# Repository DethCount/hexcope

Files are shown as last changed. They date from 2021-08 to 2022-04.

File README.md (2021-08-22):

# Hexcope - **Work in Progress**

3d printable hex pattern parabolic mirror for telescope \
20x20x20 cm parts \

## Primary mirror
19 x 20cm side hexagonal mirrors \
https://www.gifi.fr/product/id/557688/miroir-sticker-hexagonal-x-3

## Secondary mirror - **Work in Progress**
Allows for Newton setup (with basis central hex on) \

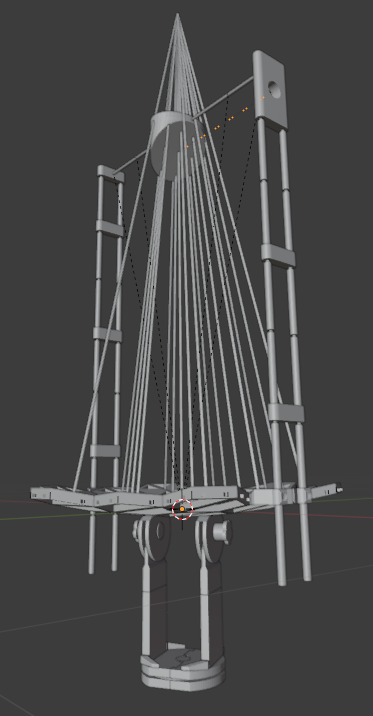
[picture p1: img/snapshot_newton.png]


or Ritchley-Chretien setup (with camera at basis center)

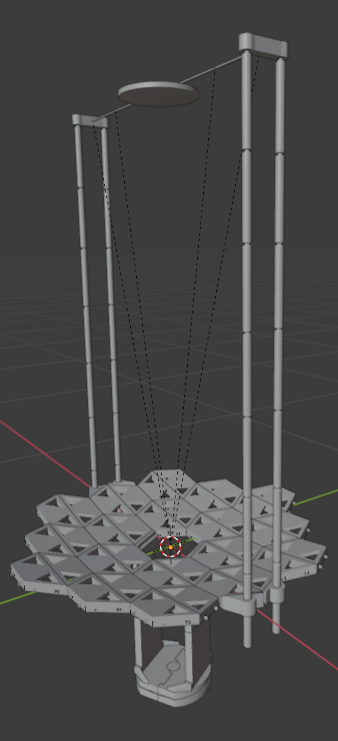
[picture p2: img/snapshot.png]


1 x 10cm radius round mirror \
https://www.gifi.fr/product/id/557686/miroir-sticker-rond-x-3

## Telescope basis
missing instrument plate and central hex for Newton setup

## Running scripts in Blender
Launch Blender (throw a terminal if you need to debug) \
in the Scripting tab open support.py and run it \
then open basis.py and run it

OR
in terminal:
blender.exe -P support.py -P basis.py

## Gcode files
DM_ is for Dagoma Magis 3d printer
DD_ is for Dagoma DiscoEasy200

## Scaling
Hexcope can be scaled by primary mirror radius hyperparameter "n" (number of hexagons) \
e.g : n = 4, f = 16 (= 1.6m) \
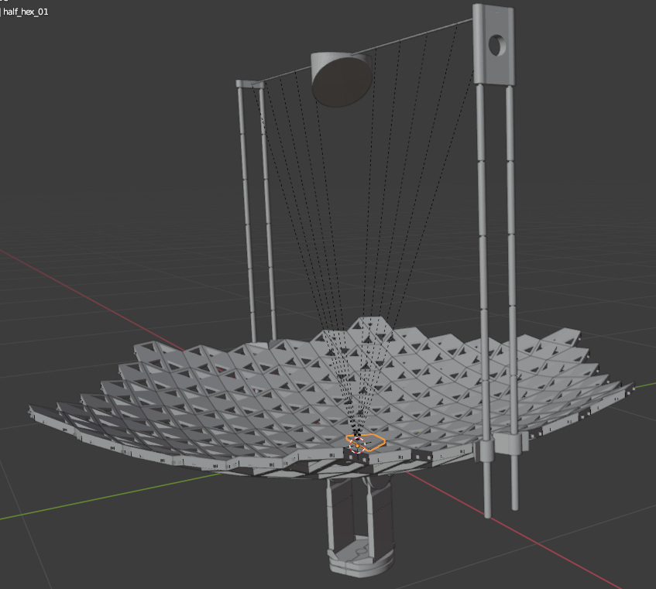
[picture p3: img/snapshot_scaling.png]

\
and by number of support arms \
e.g : support_arm_n = 6 \
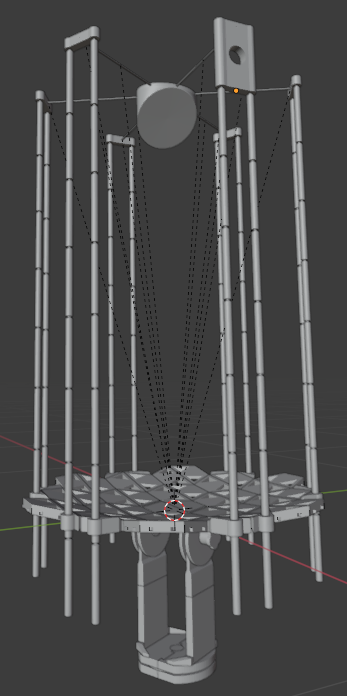
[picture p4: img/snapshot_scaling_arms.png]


## Assembling
Just clip parts together. For mirror parts, use horizontal lines, not numbers.

Primary mirror PLA parts can be soldered using filament \
https://youtu.be/Q-PgjTYsAFY

## Printing
(e.g: Dagoma DiscoEasy200) \
Layer height: 0.3mm \
Infill density: 10% \
Print speed: 75 mm/s \
Infill speed: 80 mm/s \
Outer wall speed: 50 mm/s \
Inner wall speed: 70 mm/s \
Top / Bottom speed: 70 mm/s \
Travel speed: 100 mm/s \
Initial layer speed: 20 mm/s \
Number of slower layers: 1 \
Support: touching buildplate \
Build plate adhesion type: skirt \
Skirt line count: 3 \
Skirt distance: 2mm \

- Basis: 1.326kg, 490m, 64h30
    - 2 x plate bottom: 96g, 33m, 3h30
    - 1 x plate axis: 205g, 70m, 7h
    - 2 x plate top: 96g, 33m, 3h30
    - 2 x leg: 113g, 39m, 5h  (support: everywhere)
    - 4 x foot: 10g, 4m, 0h30
    - 2 x arm: 79g, 27m, 4h
    - 2 x wheel: 135g, 46m, 6h (print vertically, bottom up)
    - 2 x screw: 18g, 6m, 2h30 (0.1mm layer height)
    - 2 x screw cap: 25g, 9m, 3h30  (0.1mm layer height)
- Primary mirror (n=0, newton): 1152g, 396m, 51h
    - 2 x center half hex: 47g, 16m, 1h30
    - 16 x half hex: 67g, 23m, 3h
- OR Primary mirror (n=1, newton): 2506g, 860m, 111h
    - 2 x center half hex: 47g, 16m, 1h30
    - 36 x half hex: 67g, 23m, 3h
- Secondary mirror support (n=0, f=16, arm_n=2, newton): 0,795kg, 300m, 100h30
    - 4 x arm block: 22g, 8m, 1h
    - 30 x arm: 18g, 7m, 2h30 (orientation: bottom up, layer height: 0.1mm, experimental: use adaptative layers, infill density: 30%)
    - 1 x arm head 0 with eyepiece support: 128g, 44m, 15h30 (orientation: little spider screw up, layer height: 0.1mm, support: touching buildplate)
    - 1 x arm head: 34g, 12m, 4h30 (orientation: little spider screw up, layer height: 0.1mm)
    - 1 x 2 spider arms 0: 5g, 2m, 1h30 (orientation: bottom up, layer height: 0.1mm, experimental: use adaptative layers, infill density: 30%)
- OR Secondary mirror support (n=1, f=16, arm_n=2, newton): 0,800kg, 302m, 102h
    - 4 x arm block: 22g, 8m, 1h
    - 30 x arm: 18g, 7m, 2h30 (orientation: bottom up, layer height: 0.1mm, experimental: use adaptative layers, infill density: 30%)
    - 1 x arm head 0 with eyepiece support: 128g, 44m, 15h30 (orientation: little spider screw up, layer height: 0.1mm, support: touching buildplate)
    - 1 x arm head: 34g, 12m, 4h30 (orientation: little spider screw up, layer height: 0.1mm)
    - 1 x 2 spider arms 0: 5g, 2m, 1h30 (orientation: bottom up, layer height: 0.1mm, experimental: use adaptative layers, infill density: 30%)
    - 1 x 2 spider arms 1: 5g, 2m, 1h30 (orientation: bottom up, layer height: 0.1mm, experimental: use adaptative layers, infill density: 30%)
- Secondary mirror (f=16, arm_n=2, newton): 177g, 60m, 16h (disable support, experimental: use adaptative layers, layer height: 0.1mm)

## Current prototype state
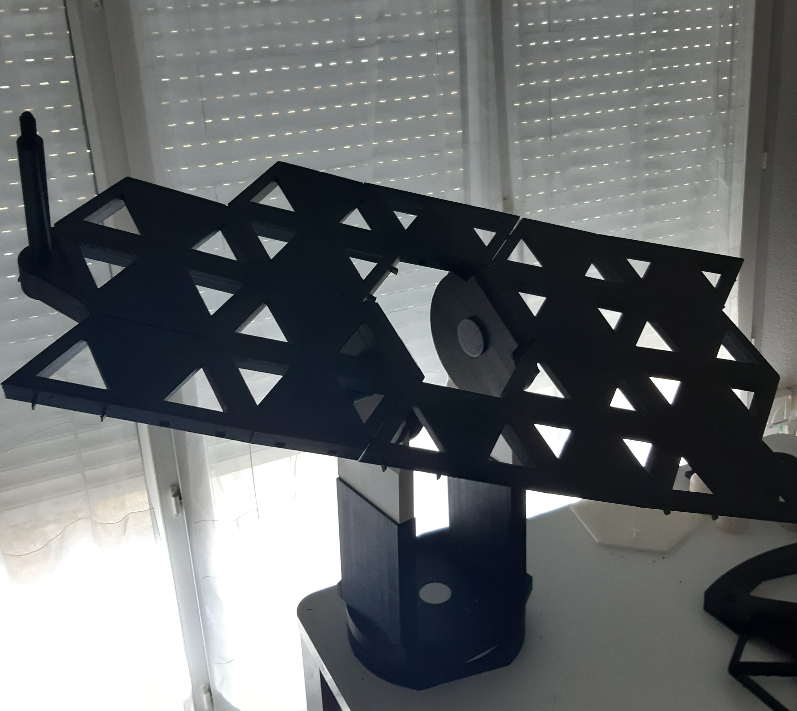
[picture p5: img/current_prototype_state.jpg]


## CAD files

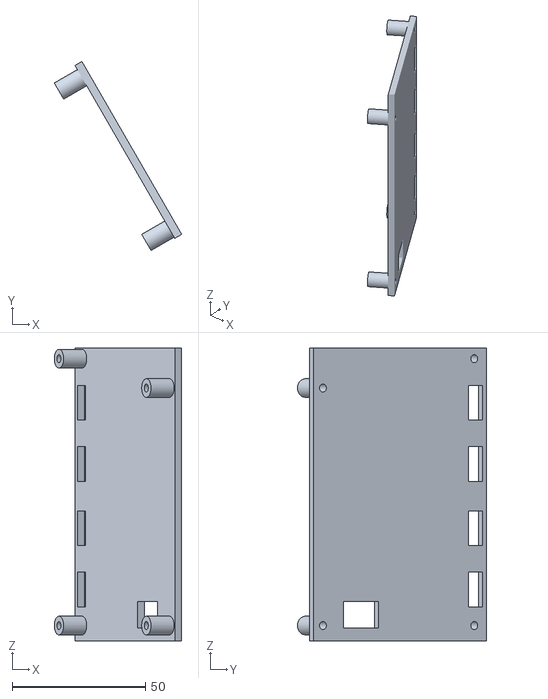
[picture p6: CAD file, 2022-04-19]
stl/basis_mainboard_cover.stl
47.8 x 70.8 x 109.8

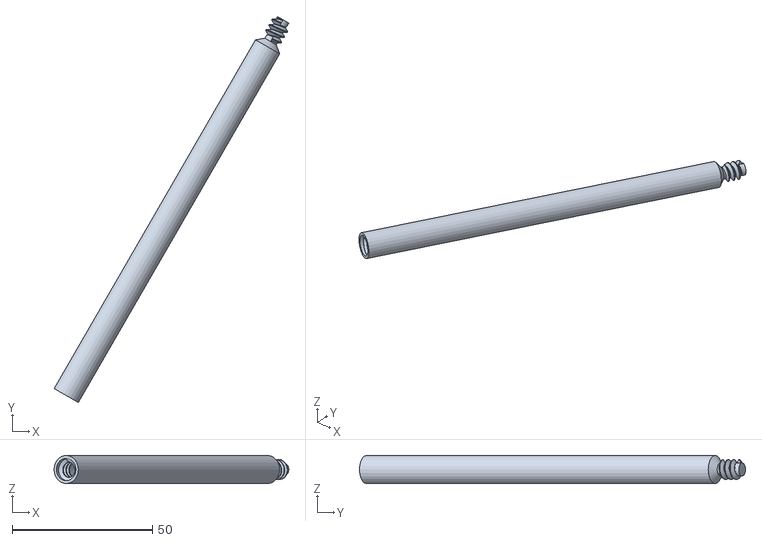
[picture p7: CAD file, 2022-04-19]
stl/support_spider_arm_4_0.stl
83.6 x 137.5 x 9.98

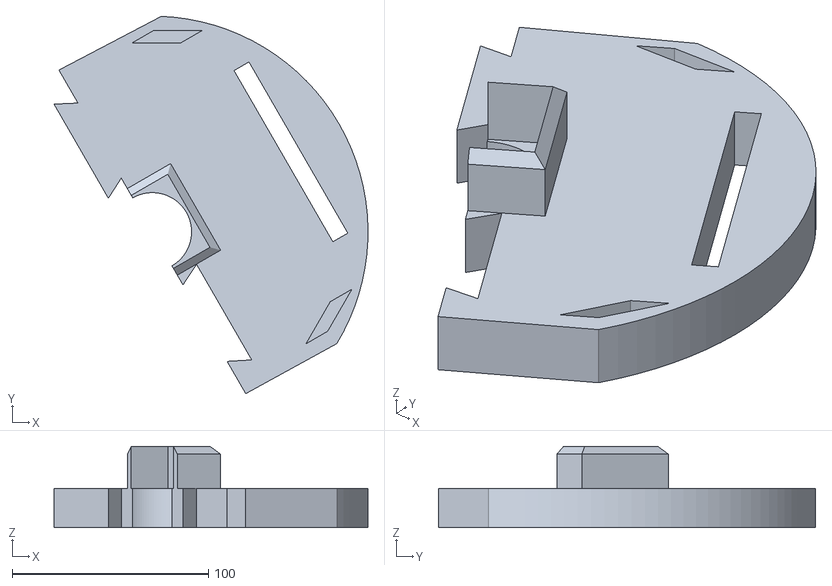
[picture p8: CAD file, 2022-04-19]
stl/basis_plate_top_r.stl
160.1 x 192.4 x 41.5

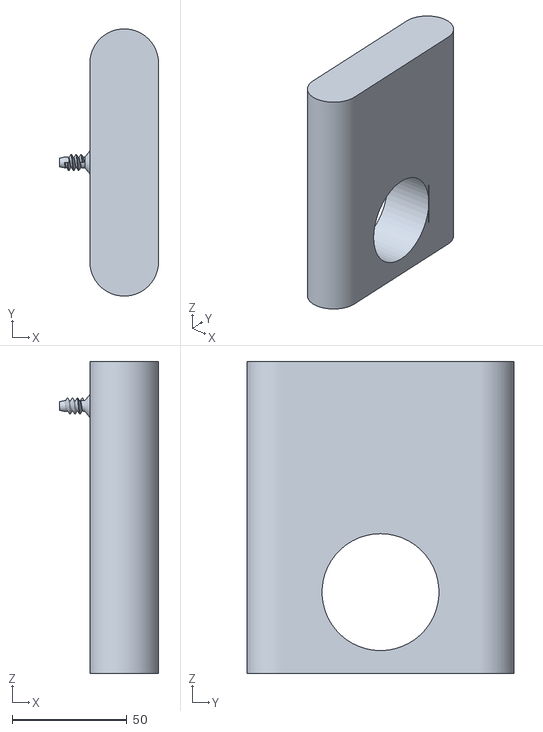
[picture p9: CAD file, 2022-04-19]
stl/support_arm_head_0.stl
43.3 x 116.6 x 136.1

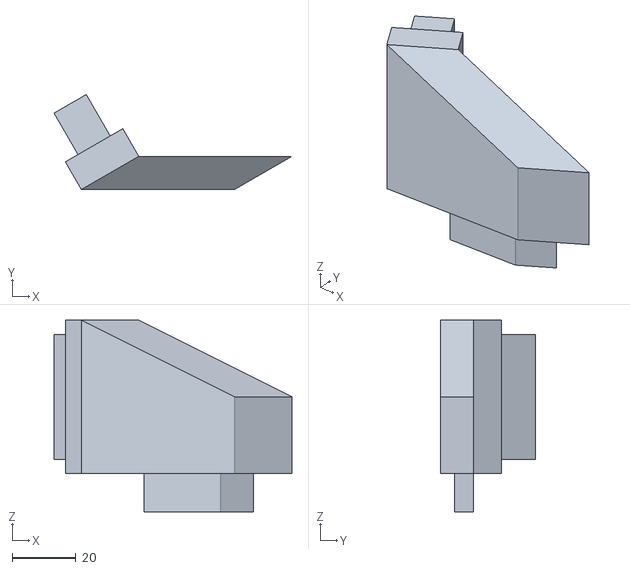
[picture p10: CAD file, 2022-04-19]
stl/basis_foot_ll.stl
74.6 x 29.8 x 60.0

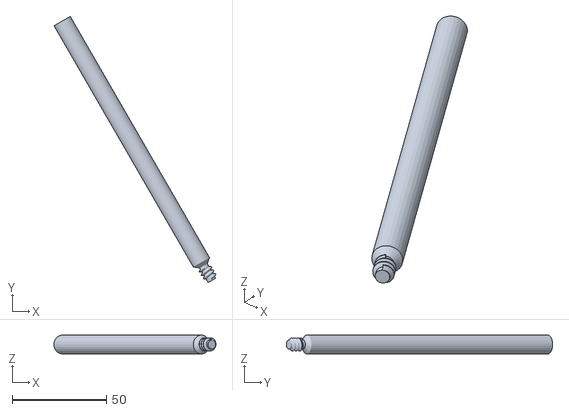
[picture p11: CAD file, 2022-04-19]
stl/support_spider_arm_2_1.stl
86.0 x 141.3 x 9.98

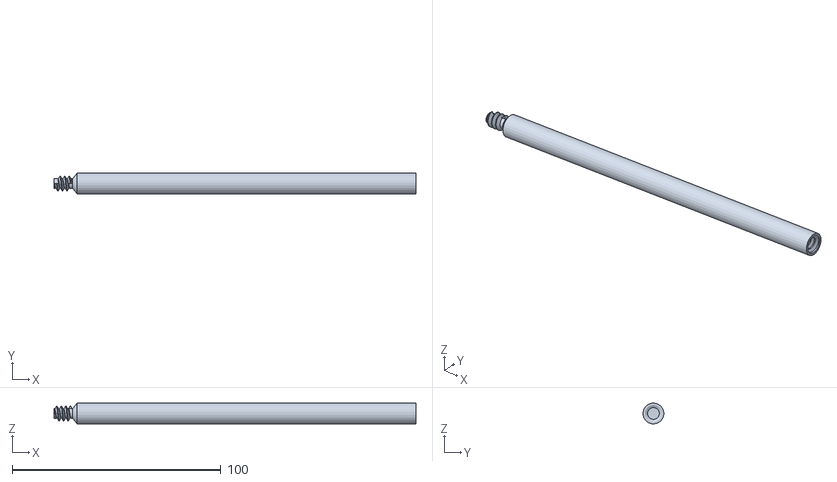
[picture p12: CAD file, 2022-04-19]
stl/support_spider_arm_0_0.stl
173.2 x 9.96 x 9.98

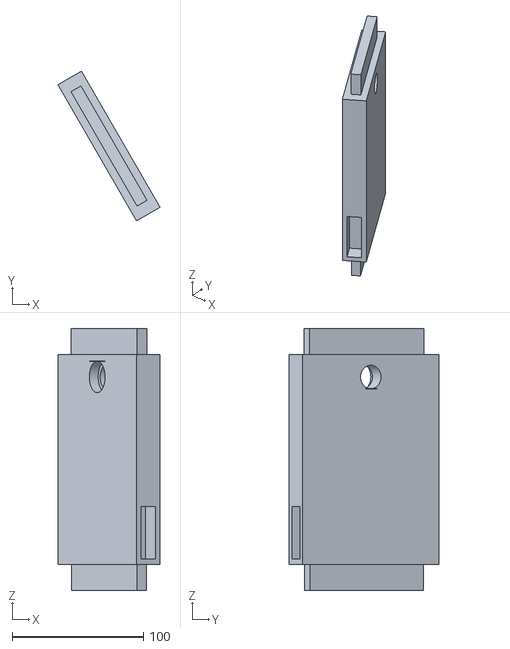
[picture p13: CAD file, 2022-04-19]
stl/basis_leg_r.stl
78.0 x 114.3 x 200.0

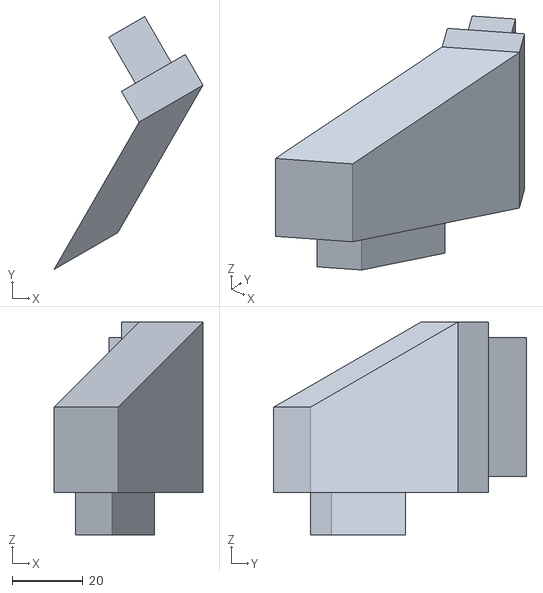
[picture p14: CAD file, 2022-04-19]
stl/basis_foot_rr.stl
42.0 x 71.3 x 60.0

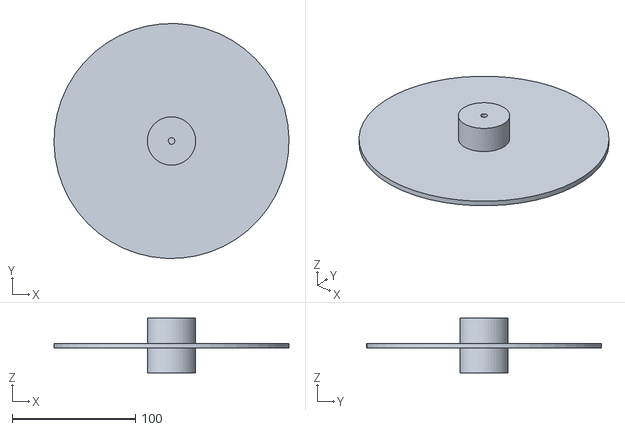
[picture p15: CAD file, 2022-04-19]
stl/basis_plate_axis.stl
190.5 x 190.4 x 44.4

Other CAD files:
stl/support_spider_arm_5_0.stl
stl/support_spider_arm_2_0.stl
stl/basis_plate_top_l.stl
stl/support_spider_arm_1_0.stl
stl/support_spider_arm_5_1.stl
stl/support_spider_arm_1_1.stl
stl/basis_foot_rl.stl
stl/basis_foot_lr.stl
learning_geometry_nodes.blend
stl/basis_arm_l.stl
stl/basis_arm_r.stl
stl/basis_cap_l.stl
stl/basis_cap_r.stl
stl/basis_leg_l.stl
stl/basis_plate_bottom_l.stl
stl/basis_plate_bottom_r.stl
stl/basis_screw_l.stl
stl/basis_screw_r.stl
stl/basis_wheel_l.stl
stl/basis_wheel_r.stl
stl/support_arm.stl
stl/support_arm_block_0_l.stl
stl/support_arm_block_0_r.stl
stl/support_arm_block_1_0_l.stl
stl/support_arm_block_1_0_r.stl
stl/support_arm_block_1_1_l.stl
stl/support_arm_block_1_1_r.stl
stl/support_arm_block_1_l.stl
stl/support_arm_block_1_r.stl
stl/support_arm_head_1.stl
stl/support_arm_head_2.stl
stl/support_arm_separator.stl
stl/support_half_hex_01.stl
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

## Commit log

2021-06-12 telescope basis wheel first part
    [basis_Camera.stl, basis_Light.stl, basis_basis_wheel_l.stl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]
2021-06-12 basis wheel part 2
    [basis_basis_wheel_l.stl, basis_basis_wheel_l_bottom.stl, basis_basis_wheel_r.stl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]
2021-06-13 basis wheel pivot hole
2021-06-13 update basis wheel stl + gcode
    [basis_basis_wheel_l.stl, basis_basis_wheel_l_bottom.stl, basis_basis_wheel_r.stl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]
2021-06-15 adding mirror support screw holes
    [support_tri_0.stl, support_tri_0_001.stl, support_tri_0_002.stl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]
2021-06-15 mirror support screw holes : gcode update
2021-06-16 basis arm
    [basis_basis_arm_l.stl, basis_basis_arm_r.stl]
2021-06-16 bugfix basis arm tooth position + added basis leg
    [basis_basis_arm_l.stl, basis_basis_arm_r.stl, basis_basis_leg_l.stl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]
2021-06-16 added Cura Dagoma Magis starting and ending gcodes + bugfix non manifold basis leg + added basis leg gcode
    [basis_basis_leg_l.stl, basis_basis_leg_r.stl]
2021-06-17 side teeth on basis leg
    [basis_basis_leg_l.stl, basis_basis_leg_r.stl]
2021-06-17 basis feet
    [basis_basis_foot_ll.stl, basis_basis_foot_lr.stl, basis_basis_foot_rl.stl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]
2021-06-18 bugfix foot teeth coudnt enter build volume + added basis top plate
    [basis_basis_foot_ll.stl, basis_basis_foot_lr.stl, basis_basis_foot_rl.stl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]
2021-06-19 bugfix space between top plate parts
    [basis_basis_plate_top_l.stl, basis_basis_plate_top_r.stl]
2021-06-19 bugfix leg bottom tooth thickness
    [basis_basis_leg_l.stl, basis_basis_leg_r.stl]
2021-06-20 bugfix leg top tooth thickness
    [basis_basis_leg_l.stl, basis_basis_leg_r.stl]
2021-06-20 basis leg top tooth margin
    [basis_basis_leg_l.stl, basis_basis_leg_r.stl]
2021-06-21 stronger design
    [basis_basis_arm_l.stl, basis_basis_arm_r.stl, basis_basis_foot_ll.stl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]
2021-06-21 basis bottom plate
    [basis_basis_plate_bottom_l.stl, basis_basis_plate_bottom_r.stl]
2021-06-21 basis plate axis
    [basis_basis_plate_axis.stl]
2021-06-22 wheel top: preparing for instrument support plate
    [basis_basis_wheel_l.stl, basis_basis_wheel_r.stl]
2021-06-22 wheel bottom: preparing for instrument support plate
    [basis_basis_wheel_l_bottom.stl, basis_basis_wheel_r_bottom.stl]
2021-06-23 forgot to update bottom plate models
    [basis_basis_plate_bottom_l.stl, basis_basis_plate_bottom_r.stl]
2021-06-24 better triangles + preparing secondary mirror
    [support_tri_0.stl, support_tri_0_001.stl, support_tri_0_002.stl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]
2021-06-26 delta secondary support arm + head
2021-07-01 secondary mirror (unstable) + gcode for Dagoma DiscoEasy200
    [support_arm_0_l.stl, support_arm_head_0.stl, support_arm_head_1.stl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]
2021-07-07 secondary mirror support (unstable) + screwless primary mirror
    [basis_Camera.stl, basis_Light.stl, support_Camera.stl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]
2021-07-08 adapting central hex for newton mode
    [basis_basis_wheel_l.stl, basis_basis_wheel_r.stl, support_half_hex_01.stl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]
2021-07-09 reducing basis margin + better basis wheel top
    [basis_basis_arm_l.stl, basis_basis_arm_r.stl, basis_basis_foot_ll.stl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]
2021-07-10 more margin
    [basis_basis_arm_l.stl, basis_basis_arm_r.stl, basis_basis_foot_ll.stl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]
2021-07-12 breaking compatibility with Dagoma Magis : single piece support wheel + cleanup gcode
    [basis_basis_wheel_l.stl, basis_basis_wheel_l_bottom.stl, basis_basis_wheel_r.stl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]
2021-07-13 hex walls to guide soldering + using less PLA
    [support_half_hex_01.stl, support_half_hex_02.stl, support_half_hex_03.stl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]
2021-07-14 arm block (unstable)
    [support_arm_block_0_0.stl, support_arm_block_0_1.stl, support_arm_block_0_2.stl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]
2021-07-15 support arm block
    [support_arm_block_0_0.stl, support_arm_block_0_1.stl, support_arm_block_0_2.stl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]
2021-07-15 arm block optimization
    [support_arm_block_0_0.stl, support_arm_block_0_1.stl, support_arm_block_0_2.stl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]
2021-07-17 cleanup support arm block
2021-07-17 readme: current prototype state
2021-07-18 basis wheel : adding external hex walls
    [basis_basis_wheel_l.stl, basis_basis_wheel_r.stl]
2021-07-19 basis wheel and arm
    [basis_basis_arm_l.stl, basis_basis_arm_r.stl, basis_basis_foot_ll.stl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]
2021-07-19 update current prototype state
2021-07-20 basis screw
    [basis_basis_screw_l.stl, basis_basis_screw_r.stl]
2021-07-20 half hex center for newton mode : more tolerance
    [support_half_hex_01.stl, support_half_hex_02.stl, support_half_hex_center.stl]
2021-07-21 basis screw cap + printing details
    [basis_cap_l.stl, basis_cap_r.stl]
2021-07-23 bugfixing clip and arm block and half hex
2021-07-26 clipping parts instead of soldering
    [basis_arm_l.stl, basis_arm_r.stl, basis_basis_arm_l.stl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]
2021-07-26 screw functions + bugfix basis screw
    [basis_cap_l.stl, basis_cap_r.stl, basis_screw_l.stl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]
2021-07-26 printing params
2021-07-26 correctly flipping normals
    [basis_arm_l.stl, basis_arm_r.stl, basis_cap_l.stl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]
2021-07-28 metric units + metric units screws + basis srews and caps + support arm (still buggy normals and screw start)
    [basis_arm_l.stl, basis_arm_r.stl, basis_cap_l.stl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]
2021-07-31 better clips
    [basis_wheel_l.stl, basis_wheel_r.stl, support_arm_block_0_0.stl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]
2021-08-02 bugfixing screws
    [basis_cap_l.stl, basis_cap_r.stl, basis_screw_l.stl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]
2021-08-09 bugfixing screws + support arm head using screws (unstable) + bugfix support arm block clips + updating snapshots
    [basis_cap_l.stl, basis_cap_r.stl, basis_screw_l.stl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]
2021-08-10 support arm head with threads
    [support_arm_head_0.stl, support_arm_head_1.stl]
2021-08-11 run script + spider arms + support_ arm head with ocular
2021-08-12 bugfix support arms, head, spider arms and newton secondary + updating models and gcode
    [support_arm_head_0.stl, support_arm_head_1.stl, support_newton_secondary_mirror.stl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]
2021-08-13 bugfix support arm head mirrored threads
    [support_arm.stl, support_arm_head_0.stl, support_arm_head_1.stl]
2021-08-13 bugfix screws needing to be sanded
    [basis_cap_l.stl, basis_cap_r.stl, basis_screw_l.stl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]
2021-08-22 secondary mirror ray + bugfix spider arms + bugfix support arms number + modular support arm head + support arm separators + separator arms + support arm block with blocking screw (unstable)
    [basis_cap_l.stl, basis_cap_r.stl, basis_screw_l.stl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]
2022-04-19 electronics + ...
    [basis_foot_ll.stl, basis_foot_lr.stl, basis_foot_rl.stl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]
